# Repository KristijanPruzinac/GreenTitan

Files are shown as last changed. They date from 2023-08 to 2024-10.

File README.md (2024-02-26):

# GreenTitan
 GreenTitan is an open-source lawnmower project started in early 2023.
 The goal of the project is to enable makers to 3D print their own lawnmower that navigates using RTK GPS technology in well under a 1000$, because the commercial mowers are way too expensive.

The project currently uses the C94-M8P RTK GPS development board by u-blox, available through online retailers such as Mouser and others. When buying the board make sure to buy the correct variant of the board according to your region (https://www.u-blox.com/en/product/c94-m8p).



# Competition
As the project is open-source there is not much competition for it except for other open source projects. Unfortunately other projects seem to either feature software for an already made machine or only the 3d printed case, not both. My goal is to provide both with documentation to enable anyone to make it themselves.

# Credits
#### MODELS  
Ublox C94-Mp8-4 case with openings - CC BY 4.0 - Scorbin - https://www.thingiverse.com/scorbin/designs  
Einhell battery adapter - GNU GPL v3 - Hans - https://www.printables.com/social/193091-hans/about

#### SOFTWARE  
Recieve NAV_POSLLH message - iforce2d - https://www.youtube.com/watch?v=TwhCX0c8Xe0

#### LIBRARIES  
Adafruit MPU6050 - https://github.com/adafruit/Adafruit_MPU6050
AceSorting - https://github.com/bxparks/AceSorting

# Development process
The project is currently under development and expected to be finished in october.

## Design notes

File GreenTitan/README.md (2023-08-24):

# Arduino code  
This is the Arduino code for uploading to the ESP32 microcontroller.

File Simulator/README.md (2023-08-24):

# GreenTitan simulator

This is software written in Processing (java) sketchbook that is used to develop the GreenTitan project software. The issue with programming microcontrollers is often that it is harder to test them, especially with projects like robotic lawnmowers. It is for this reason that I decided to make this simulator so I can test mower software before deploying it with ESP32.

Feel free to use this if it is helpful to you in any way.



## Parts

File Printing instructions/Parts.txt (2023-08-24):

2x GW370 DC Worm Gear Motor (12V / 80RPM)
2x Shopping cart wheel (Height must be 10cm, Diameter when rotated should be less than 13cm, top hole should be less than 1cm)
1x C94 M8P RTK GPS (Choose correct region when buying)
M3 Allen screw 10mm & nut, 20x (8x)
M4 Allen screw 25mm & nut, 40x (34x)

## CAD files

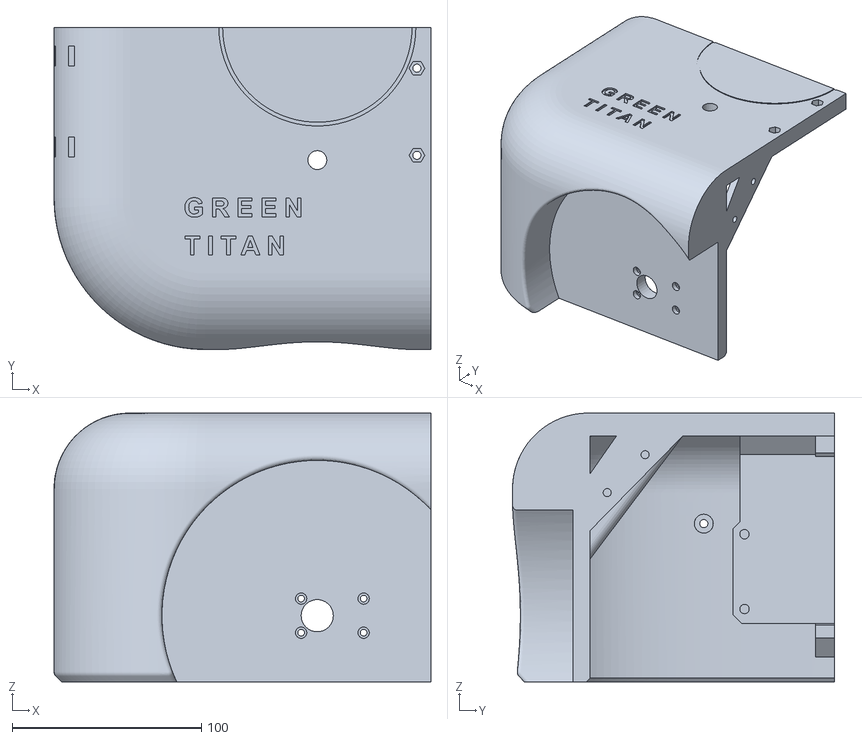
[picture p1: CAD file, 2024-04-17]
Printing instructions/Frame/Back/Right.stl
199.1 x 170.0 x 142.0

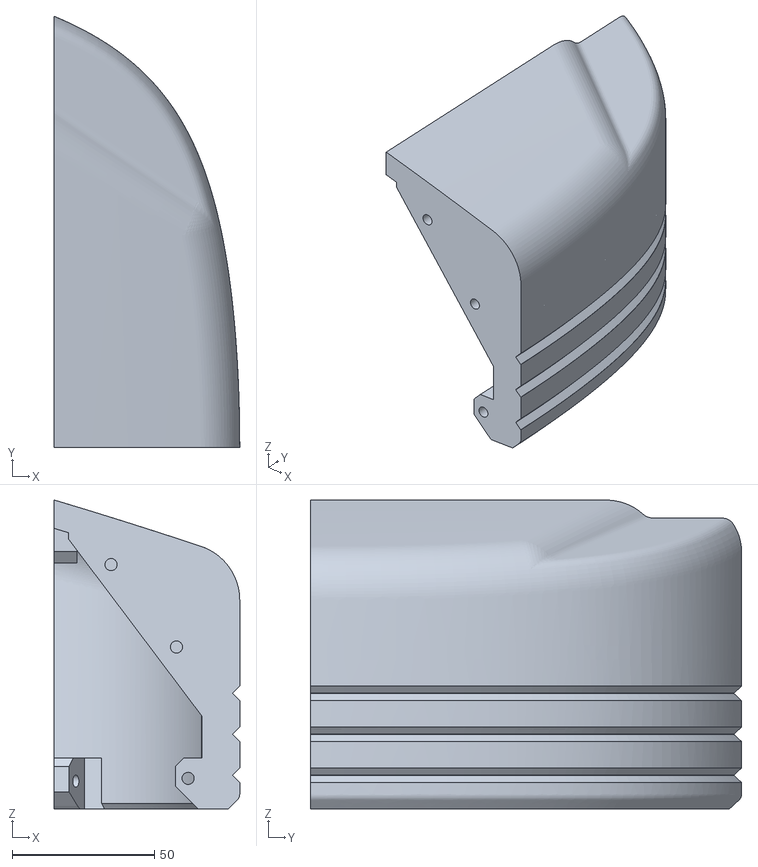
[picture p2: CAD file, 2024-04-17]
Printing instructions/Frame/Front/GreenTitanBumperLeft.stl
65.3 x 151.8 x 108.7

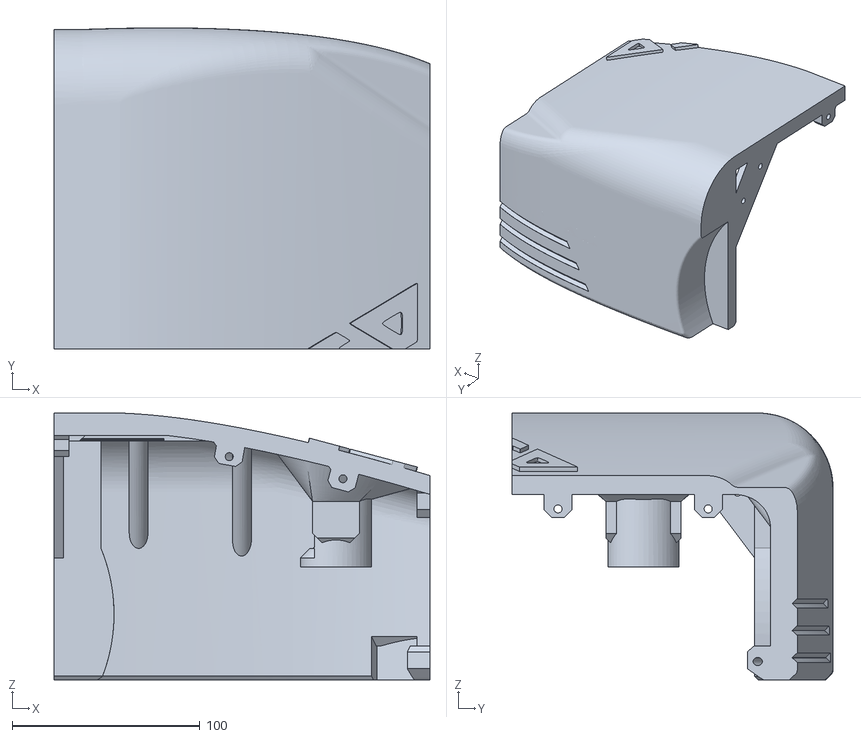
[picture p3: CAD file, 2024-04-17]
Printing instructions/Frame/Midsection/GreenTitanMidsectionLeft.stl
200.0 x 170.8 x 142.0

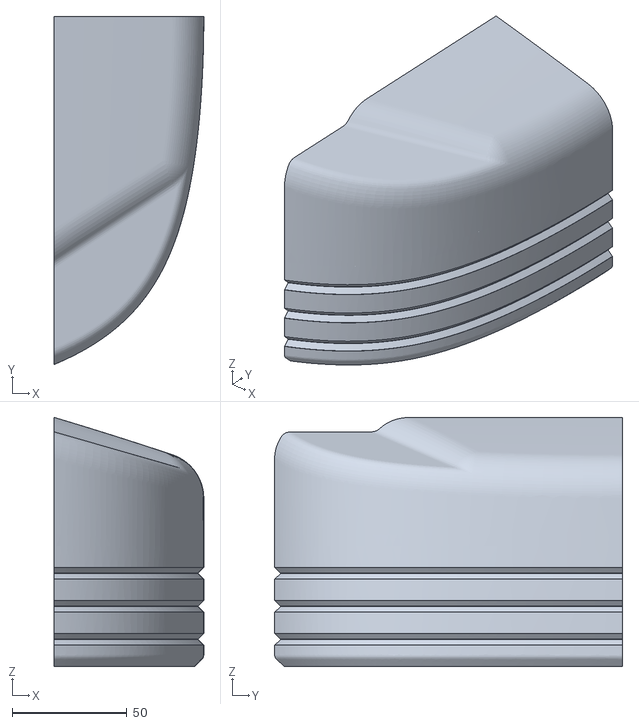
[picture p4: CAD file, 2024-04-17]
Printing instructions/Frame/Front/GreenTitanBumperRight.stl
65.3 x 151.8 x 108.7

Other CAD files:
Printing instructions/Frame/Back/Left.stl
Printing instructions/Frame/Midsection/GreenTitanMidsectionRight.stl

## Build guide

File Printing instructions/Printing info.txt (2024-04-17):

Used Ultimaker Cura 5.4.0 slicer

-----------------------------------------------------
REQUIRED

Minimum build plate area - 20cm * 20cm

-----------------------------------------------------
PRINT SETTINGS

Top / Bottom - 2 layers each
0.3mm layer height
Adhesion - Brim
Infill pattern - lines
Material - PLA, 200deg print temperature

-----------------------------------------------------
PART SETTINGS

Double battery adapter (Einhell) - Weight 24g, Printing time 1:30 | Infill 30%
C94 M8P Case - Weight 20g, Printing time 0:47 | Infill 20%

GENERAL SETTINGS: Infill 10% | Enable supports, Support placement Everywhere, Support structure Normal, Enable Support inteface False, Support density 10%, SUpport Z distance 0.3, Support XY distance 1.2

FRAME Front bumper - Weight 135g, Printing time 6:53
Support placement: Touching buildplate
Minimum support area: 500mm2

FRAME Side - Weight 360g, Printing time 18:49
Support placement: Everywhere
Minimum support area: 100mm2

FRAME Back - 353g, Printing time 20:28

Adjust minimum support area so supports are generated properly, but small holes aren't filled with supports (It is a pain to remove)

-----------------------------------------------------
ADVICE

Print every part so its interior side is facing the build plate, when supports are used on the exterior it looks pretty bad

The only parts I printed with exterior side facing build plate are the 2 back pieces and I printed their charging port facing the build plate, it looks tolerable

-----------------------------------------------------

TOTAL PLASTIC REQUIRED - LESS THAN 3KG

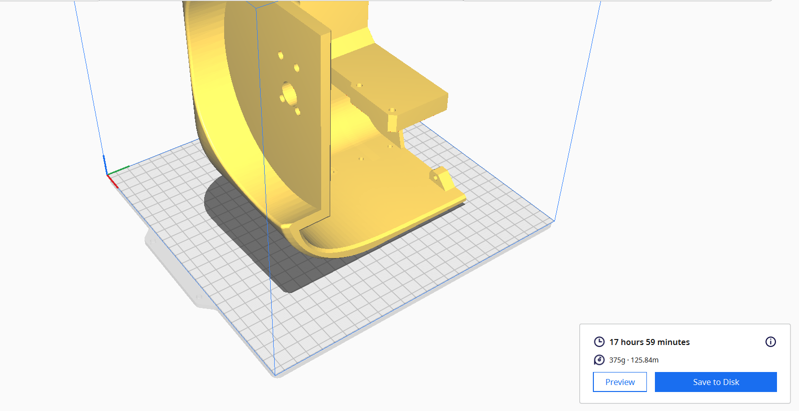
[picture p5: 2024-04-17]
Printing instructions/Frame/Back/Orientation.png

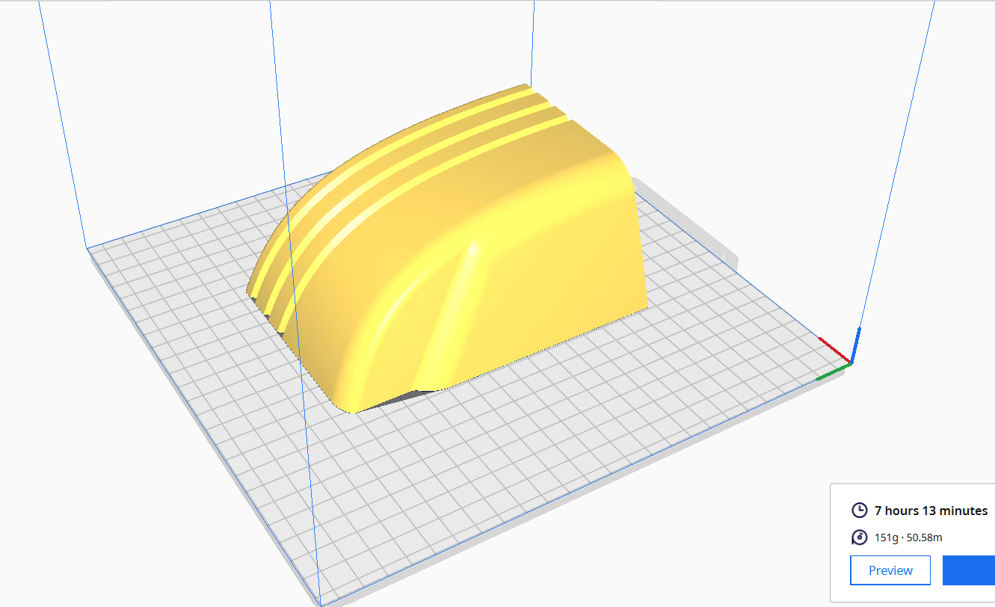
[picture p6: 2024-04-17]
Printing instructions/Frame/Front/Orientation.png

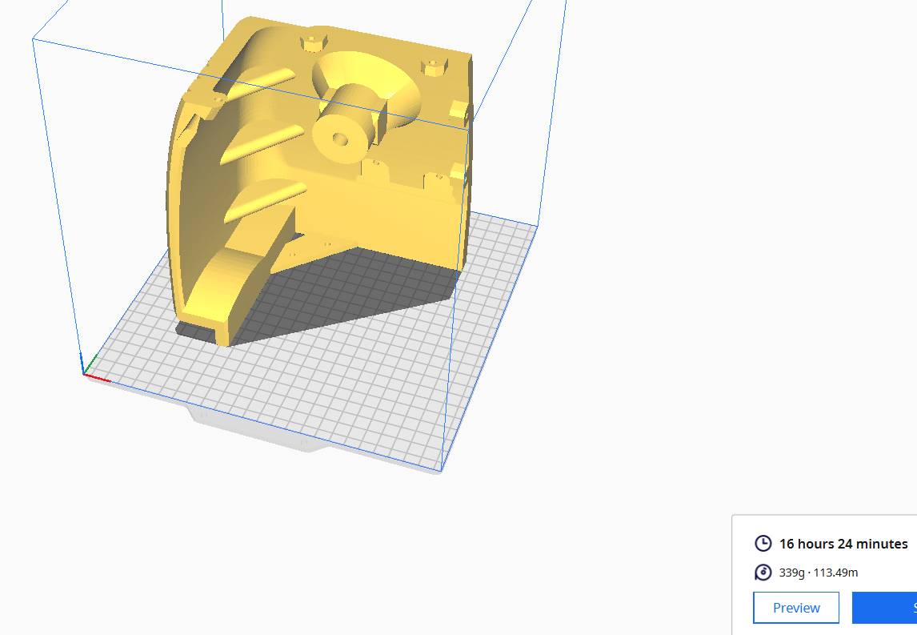
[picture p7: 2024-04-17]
Printing instructions/Frame/Midsection/Orientation.png

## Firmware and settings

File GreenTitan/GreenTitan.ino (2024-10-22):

// -------------------------------------------------------- DEFINITIONS ---------------------------------------------------------------
#include "Defines.h"

// -------------------------------------------------------- STATUS INDICATORS ---------------------------------------------------------------

int STATUS_BATTERY_LOW = false;
int STATUS_BATTERY_CHARGED = false;
int GPS_ACCURACY_STABLE = false;

// -------------------------------------------------------- CONFIGURATION ---------------------------------------------------------------

bool CONFIG_PATH = false;
bool CONFIG_BATTERY = false;
bool CONFIG_MOTORS = false;
bool CONFIG_GYRO = false;
bool CONFIG_RAIN_SENSOR = false;

// -------------------------------------------------------- GLOBALS ---------------------------------------------------------------

bool SETUP_COMPLETED = true;

int MOWER_OVERLAP = 15; //In cm
int MAX_DEVIATION = 50;
int BASE_LON = -5672328;
int BASE_LAT = 3376391;
int BASE_EXIT_LON = -5672328;
int BASE_EXIT_LAT = 3376391;

int GPS_ACC_THRESHOLD = 18;
int GPS_STABILITY_CHECK_DURATION = 300; //5 minutes

float BATTERY_LEVEL_MIN = 16;
float BATTERY_LEVEL_MAX = 18;

bool MOTOR_SIDE_INVERT = true;
bool MOTOR_LEFT_INVERT = true;
bool MOTOR_RIGHT_INVERT = false;
float MOTOR_OPTIMAL_VOLTAGE = 12;

//TODO: ADD TO CONFIG
bool IMU_INVERT = false;
float MOTION_ACC_FACTOR = 1.0;

SemaphoreHandle_t IMUMutex;
SemaphoreHandle_t GPSMutex;
SemaphoreHandle_t MotionMutex;

// -------------------------------------------------------- DEPENDENCIES ---------------------------------------------------------------

//Peripherals
#include "IMU.h"
#include "GPS.h"
#include "Battery.h"
#include "RainSensor.h"

//Program dependencies
#include "Functions.h"
#include "Algorithm.h"
#include "Configuration.h"

//Tasks
#include "MotionTask.h"
#include "BluetoothTask.h"
#include "SensorsTask.h"
#include "Motor.h"

// -------------------------------------------------------- INIT FUNCTIONS ---------------------------------------------------------------

void InitFreeRtos(){
  IMUMutex = xSemaphoreCreateMutex();
  GPSMutex = xSemaphoreCreateMutex();
  MotionMutex = xSemaphoreCreateMutex();

  //Motor task
  xTaskCreatePinnedToCore (
    MotorTask,     // Function to implement the task
    "MotorTask",   // Name of the task
    8192,      // Stack size in bytes
    NULL,      // Task input parameter
    2,         // Priority of the task
    NULL,      // Task handle.
    0          // Core where the task should run
  );

  //IMU task
  xTaskCreatePinnedToCore (
    IMUTask,     // Function to implement the task
    "IMUTask",   // Name of the task
    8192,      // Stack size in bytes
    NULL,      // Task input parameter
    2,         // Priority of the task
    NULL,      // Task handle.
    0          // Core where the task should run
  );

  //Sensors task
  xTaskCreatePinnedToCore (
    SensorsTask,     // Function to implement the task
    "SensorsTask",   // Name of the task
    8192,      // Stack size in bytes
    NULL,      // Task input parameter
    2,         // Priority of the task
    NULL,      // Task handle.
    0          // Core where the task should run
  );

  //Motion task
  xTaskCreatePinnedToCore (
    MotionTask,     // Function to implement the task
    "MotionTask",   // Name of the task
    8192,      // Stack size in bytes
    NULL,      // Task input parameter
    1,         // Priority of the task
    NULL,      // Task handle.
    0          // Core where the task should run
  );

  //Bluetooth task
  xTaskCreatePinnedToCore (
    BluetoothTask,     // Function to implement the task
    "BluetoothTask",   // Name of the task
    8192,      // Stack size in bytes
    NULL,      // Task input parameter
    0,         // Priority of the task
    NULL,      // Task handle.
    0          // Core where the task should run
  );
}

extern void InitMotors();
extern bool InitIMU();
extern void InitGPS();
extern void InitBattery();
extern void InitRainSensor();

// -------------------------------------------------------- PROGRAM START ---------------------------------------------------------------
void setup() {
  Serial.begin(SERIAL_BAUDRATE);
}

String Mode = "POWER_ON";
/*
POWER_ON

SETUP

START
RUNNING PAUSE
STOP
CHARGING
*/

void MainCharging();
void MainChargingStart();
void MainChargingStop();
void MainStop();
void MainPause();
void MainStart();
void MainRunning();
void MainPowerOn();
void MainSetup();

void loop(){
  if (Mode == "POWER_ON"){
    FileResult result = InitConfiguration();
    if (result != SUCCESS){
      Error("Configuration failed to initialize with error " + String(result));
    }

    Serial.println("Configuration loaded!");

    delay(200);

    InitMotors();
    if (!InitIMU()){
      Error("Gyro failed to initialize!");
    }
    //InitGPS();
    InitBattery();
    InitRainSensor();

    Serial.println("Peripherals initialized!");

    delay(200);

    if (!InitBluetooth()){
      Error("Bluetooth failed to initialize!");
    }
    else {
      Serial.println("Bluetooth initialized!");
    }

    delay(200);

    InitFreeRtos();

    Serial.println("FreeRtos initialized!");

    //TODO: Move to setup
    IMUCalibrate();

    delay(500);
    if (SETUP_COMPLETED){
      Mode = "RUNNING";
    }
    else {
      Mode = "SETUP";
    }
  }
  else if (Mode == "SETUP"){

  }
  else if (Mode == "START"){
    String message = BluetoothRead();

    if (message == "GPS_ACC"){
      BluetoothWrite(String(GpsGetAcc()));
    }
    else if (message == "CAPTURE_START") {
        AlgorithmCaptureStart();
        BluetoothWrite("Executed!");
    } else if (message == "GPS_POS"){
        //BluetoothWrite(String(GpsGetLon()) + " " + String(GpsGetLat()) + " " + String((int) IMUGetHeading()));
    } else if (message == "CAPTURE_BASE_POINT") {
        AlgorithmCaptureBasePoint();
        BluetoothWrite("Executed!");
    } else if (message == "CAPTURE_BASE_EXIT_POINT") {
        AlgorithmCaptureBaseExitPoint();
        BluetoothWrite("Executed!");
    } else if (message == "CAPTURE_NEW_OUTLINE") {
        AlgorithmCaptureNewOutline();
        BluetoothWrite("Executed!");
    } else if (message == "CAPTURE_NEW_POINT") {
        AlgorithmCaptureNewPoint();
        BluetoothWrite("Executed!");
    } else if (message == "REMOVE_OUTLINE") {
        bool result = AlgorithmCaptureRemoveOutline();
        BluetoothWrite(String(result));
    } else if (message == "REMOVE_POINT") {
        bool result = AlgorithmCaptureRemovePoint();
        BluetoothWrite(String(result));
    } else if (message == "CAPTURE_END") {
        bool result = AlgorithmCaptureEnd();
        BluetoothWrite(String(result));
    } else if (message == "GET_PATH_STRING"){
        BluetoothWrite(AlgorithmGetPathString());
    } else if (message == "SAVE_CONFIGURATION"){
        FileResult result = SaveConfiguration();
        BluetoothWrite(String(result));
    } else if (message == "MOWER_START"){
      Mode = "RUNNING";
    } else if (message == "TEST" || message == "GPS/GET/ACCURACY"){
      MotionSetTarget(GpsGetLon(), GpsGetLat() + 800);
    }
  }
  else if (Mode == "RUNNING"){
    MotorDriveAngle(0, FORWARD, 1.0);
    delay(1000);
    MotionSetTarget(1, -101);
    while (MowerIsInMotion()){
      delay(10);
    }
    MotorDriveAngle(0, FORWARD, 1.0);
    delay(1000);

    while (1){
      delay(100);
    }
  }
  delay(10);
}

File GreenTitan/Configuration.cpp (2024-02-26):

#include "Configuration.h"

#define FORMAT_LITTLEFS_IF_FAILED true

FileResult listDir(fs::FS &fs, const char *dirname, uint8_t levels) {
    File root = fs.open(dirname);
    if (!root) {
        return FAILED_OPEN;
    }
    if (!root.isDirectory()) {
        return NOT_A_DIRECTORY;
    }

    File file = root.openNextFile();
    while (file) {
        if (file.isDirectory()) {
            FileResult result = listDir(fs, file.path(), levels - 1);
            if (result != SUCCESS) {
                return result;
            }
        }
        file = root.openNextFile();
    }

    return SUCCESS;
}

FileResult createDir(fs::FS &fs, const char *path) {
    if (fs.mkdir(path)) {
        return SUCCESS;
    } else {
        return MKDIR_FAILED;
    }
}

FileResult removeDir(fs::FS &fs, const char *path) {
    if (fs.rmdir(path)) {
        return SUCCESS;
    } else {
        return RMDIR_FAILED;
    }
}

FileResult readFile(fs::FS &fs, const char *path, String &fileContent) {
    File file = fs.open(path);
    if (!file || file.isDirectory()) {
        return FAILED_OPEN;
    }

    while (file.available()) {
        char c = file.read();
        fileContent += c;
    }
    file.close();

    return SUCCESS;
}

FileResult writeFile(fs::FS &fs, const char *path, const char *message) {
    File file = fs.open(path, FILE_WRITE);
    if (!file) {
        return FAILED_OPEN;
    }
    if (file.print(message)) {
        file.close();
        return SUCCESS;
    } else {
        file.close();
        return FAILED_WRITE;
    }
}

FileResult appendFile(fs::FS &fs, const char *path, const char *message) {
    File file = fs.open(path, FILE_APPEND);
    if (!file) {
        return FAILED_OPEN;
    }
    if (file.print(message)) {
        file.close();
        return SUCCESS;
    } else {
        file.close();
        return APPEND_FAILED;
    }
}

FileResult renameFile(fs::FS &fs, const char *path1, const char *path2) {
    if (fs.rename(path1, path2)) {
        return SUCCESS;
    } else {
        return RENAME_FAILED;
    }
}

FileResult deleteFile(fs::FS &fs, const char *path) {
    if (fs.remove(path)) {
        return SUCCESS;
    } else {
        return DELETE_FAILED;
    }
}

FileResult InitConfiguration(){
  if(!LittleFS.begin(FORMAT_LITTLEFS_IF_FAILED)){
    return INIT_FAILED;
  }

  LoadConfiguration();

  return SUCCESS;
}

FileResult SaveConfiguration() {
    String ConfigWriteString = "";
    ConfigWriteString += "SETUP_COMPLETED " + String(SETUP_COMPLETED) + "\n";
    ConfigWriteString += "MOWER_OVERLAP " + String(MOWER_OVERLAP) + "\n";
    ConfigWriteString += "MAX_DEVIATION " + String(MAX_DEVIATION) + "\n";
    ConfigWriteString += "BASE_LON " + String(BASE_LON) + "\n";
    ConfigWriteString += "BASE_LAT " + String(BASE_LAT) + "\n";
    ConfigWriteString += "BASE_EXIT_LON " + String(BASE_EXIT_LON) + "\n";
    ConfigWriteString += "BASE_EXIT_LAT " + String(BASE_EXIT_LAT) + "\n";
    ConfigWriteString += "GPS_ACC_THRESHOLD " + String(GPS_ACC_THRESHOLD) + "\n";
    ConfigWriteString += "GPS_STABILITY_CHECK_DURATION " + String(GPS_STABILITY_CHECK_DURATION) + "\n";
    ConfigWriteString += "BATTERY_LEVEL_MIN " + String(BATTERY_LEVEL_MIN) + "\n";
    ConfigWriteString += "BATTERY_LEVEL_MAX " + String(BATTERY_LEVEL_MAX) + "\n";
    ConfigWriteString += "MOTOR_SIDE_INVERT " + String(MOTOR_SIDE_INVERT) + "\n";
    ConfigWriteString += "MOTOR_LEFT_INVERT " + String(MOTOR_LEFT_INVERT) + "\n";
    ConfigWriteString += "MOTOR_RIGHT_INVERT " + String(MOTOR_RIGHT_INVERT) + "\n";
    ConfigWriteString += "MOTOR_OPTIMAL_VOLTAGE " + String(MOTOR_OPTIMAL_VOLTAGE) + "\n";
    
    //Config status
    ConfigWriteString += "CONFIG_PATH " + String(CONFIG_PATH) + "\n";
    ConfigWriteString += "CONFIG_BATTERY " + String(CONFIG_BATTERY) + "\n";
    ConfigWriteString += "CONFIG_MOTORS " + String(CONFIG_MOTORS) + "\n";
    ConfigWriteString += "CONFIG_GYRO " + String(CONFIG_GYRO) + "\n";
    ConfigWriteString += "CONFIG_RAIN_SENSOR " + String(CONFIG_RAIN_SENSOR) + "\n";

    //Outlines
    ConfigWriteString += "ALGORITHM_PATH\n";
    ConfigWriteString += AlgorithmGetPathString();

    deleteFile(LittleFS, "/Configuration.txt");
    return writeFile(LittleFS, "/Configuration.txt", ConfigWriteString.c_str());
}
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

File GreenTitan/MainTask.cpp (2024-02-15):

#include "MainTask.h"

/*
int pointsCount = 0;
int gcodeIndex = 0;
int pointsX[50];
int pointsY[50];

//Parse bluetooth messages
void MainParseBluetooth(){
  while (true){
    String message = BluetoothRead(); if (message.length() == 0 || message.equals("")){ break; }

    //Count / characters
    int co = 0;
    for (int i = 0; i < message.length(); i++) {
      if (message.charAt(i) == '/') {
        co++;
      }
    }
    if (co < 2){break;} //Invalid message

    String MessageGroup = message.substring(0, message.indexOf('/'));
    message = message.substring(message.indexOf('/') + 1); // Update message to remove the first part

    String ActionGroup = message.substring(0, message.indexOf('/'));
    message = message.substring(message.indexOf('/') + 1); // Update message to remove the second part

    String DataGroup = message;

    //STATUS ------------------------------------------
    if (MessageGroup == "STATUS") {
      if (ActionGroup == "GET") {
        Respond("STATUS", MowerStatus);
      }
      else if (ActionGroup == "SET") {
        if (DataGroup == "RUNNING") {
          MowerResume();
        }
        else if (DataGroup == "PAUSED") {
          MowerPause();
        }

        Respond("STATUS", MowerStatus);
      }
    }
    else if (MessageGroup == "MOTOR") {
      if (ActionGroup == "SET") {
        if (DataGroup == "LEFTFORWARD") {}
        else if (DataGroup == "LEFTBACKWARD") {}
        else if (DataGroup == "LEFTSTOP") {}
        else if (DataGroup == "RIGHTFORWARD") {}
        else if (DataGroup == "RIGHTBACKWARD") {}
        else if (DataGroup == "RIGHTSTOP") {}
        else if (DataGroup == "MAINSTART") {
          MotorMainOn();
        }
        else if (DataGroup == "MAINSTOP") {
          MotorMainOff();
        }
      }
      else if (ActionGroup == "MOVE") {
        if (DataGroup == "FORWARD") {
          MotorForward();
        }
        else if (DataGroup == "BACKWARD") {
          MotorBackward();
        }
        else if (DataGroup == "ROTATELEFT") {
          MotorTurnLeft();
        }
        else if (DataGroup == "ROTATERIGHT") {
          MotorTurnRight();
        }
        else if (DataGroup == "STOP"){
          MotorStop();
        }
      }
    }
    else if (MessageGroup == "GPS"){
      if (ActionGroup == "GET") {
        if (DataGroup == "ACCURACY") {
          Respond("GPS", String(posllh.hAcc));
        }
      }
    }
    else if (MessageGroup == "GCODE"){
      if (ActionGroup == "ADD") {
        if (DataGroup == "POINT") { //ADD NEW POINT
          pointsX[pointsCount] = posllh.lon;
          pointsY[pointsCount] = posllh.lat;

          pointsCount++;
        }
      }
      else if (ActionGroup == "RESET") {
        pointsCount = 0;
      }
      else if (ActionGroup == "START") {
        MowerExecutingPath = true;
        gcodeIndex = 0;
      }
    }
  }

  return;
}
*/

//TODO: Implement functionality
String Mode = "POWER_ON";
/* CHARGING STOP PAUSE START RUNNING POWER_ON SETUP*/

void MainCharging(){}
void MainChargingStart(){
  Serial.println("Charging start");
}
void MainChargingStop(){}
void MainStop(){Serial.println("Strayed from path (STOP)");}
void MainPause(){}
void MainStart(){}
void MainRunning(){}
void MainPowerOn(){
  //LoadConfiguration();
  //GenerateGcode();
}
void MainSetup(){}

char QueueBluetoothMainReceive(){
  char returnChar = NULL;
  xQueueReceive(BluetoothMainQueue, &returnChar, 50);

  return returnChar;
}

void QueueMainBluetoothSend(char receivedChar){
  xQueueSend(BluetoothMainQueue, &receivedChar, 50);
}

void MainTask(void* pvParameters){
  while (1){
    delay(10);
  }
}

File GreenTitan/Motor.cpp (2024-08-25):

#include "Motor.h"

// create the stepper motor objects
ContinuousStepper<StepperDriver> motorA;
ContinuousStepper<StepperDriver> motorB;

float MowerAngularDegreesToMotorSteps(float unit){
  //     PATH AROUND CIRCUMFERENCE TRAVELLED (CM)                     STEPS PER CM                2 MOTORS
  return ((unit / (360.0)) * (MOTOR_DIAMETER * PI)) * (MOTOR_STEPS_PER_REV / (WHEEL_DIAMETER * PI)) / 2;
}

void MotorDriveAngle(float angle, bool forward, float speedFactor = 1) {
  // SpeedFactor
  speedFactor = constrain(speedFactor, 0.0, 1.0);

  // Angle measured from North clockwise
  angle = constrain(angle, MOTOR_ANGLE_MIN, MOTOR_ANGLE_MAX);

  // Motor activation percentages
  float motorPercentLeft = (angle + 90.0) / 180.0; motorPercentLeft = constrain(motorPercentLeft, 0, 1);
  float motorPercentRight = 1 - (motorPercentLeft); motorPercentRight = constrain(motorPercentRight, 0, 1);

  // Switch sides
  if (MOTOR_SIDE_INVERT) {
    std::swap(motorPercentLeft, motorPercentRight);
  }

  // Calculate speeds for motors
  float speedA = MOTOR_MAX_SPEED * speedFactor * motorPercentLeft;
  float speedB = MOTOR_MAX_SPEED * speedFactor * motorPercentRight;

  if (!MOTOR_LEFT_INVERT) {
    motorA.spin(forward ? speedA : -speedA);
  } else {
    motorA.spin(forward ? -speedA : speedA);
  }

  if (!MOTOR_RIGHT_INVERT) {
    motorB.spin(forward ? speedB : -speedB);
  } else {
    motorB.spin(forward ? -speedB : speedB);
  }
}

void MotorRotate(float speedFactor) {
  // SpeedFactor
  speedFactor = constrain(speedFactor, -1.0, 1.0);

  int invertA = 1;
  int invertB = 1;

  // Rotate
  if (MOTOR_SIDE_INVERT) {
    speedFactor = -speedFactor;
  }

  if (MOTOR_LEFT_INVERT) {
    invertA = -invertA;
  }
  if (MOTOR_RIGHT_INVERT) {
    invertB = -invertB;
  }
  
  motorA.spin(invertA * MOTOR_MAX_SPEED * speedFactor);
  motorB.spin(-invertB * MOTOR_MAX_SPEED * speedFactor);
}

float motorASpeed = 0;
void MotorRotateAcceleration(float acceleration){
  int invertA = 1;
  int invertB = 1;

  // Rotate
  /*
  if (MOTOR_SIDE_INVERT) {
    direction = !direction;
  }
  */

  if (MOTOR_LEFT_INVERT) {
    invertA = -invertA;
  }
  if (MOTOR_RIGHT_INVERT) {
    invertB = -invertB;
  }

  motorASpeed += MowerAngularDegreesToMotorSteps(acceleration);
  if (motorASpeed > MOTOR_MAX_SPEED / 2) motorASpeed = MOTOR_MAX_SPEED / 2;
  if (motorASpeed < -MOTOR_MAX_SPEED / 2) motorASpeed = -MOTOR_MAX_SPEED / 2;

  if (motorASpeed > 0){
    motorA.spin(invertA * motorASpeed);
    motorB.spin(-invertB * motorASpeed);
  }
  else if (motorASpeed < 0) {
    motorA.spin(-invertA * motorASpeed);
    motorB.spin(invertB * motorASpeed);
  }
  else {
    motorA.stop();
    motorB.stop();
  }

  Serial.print(motorA.speed()); Serial.print(" "); Serial.println(motorB.speed());

  //Serial.println(motorASpeed);
  //Serial.println(motorA.getCurrentVelocityInStepsPerSecond());
}

void InitMotors() {
  pinMode(MOTOR_MAIN, OUTPUT);

  motorA.begin(MOTOR_A_STEP_PIN, MOTOR_A_DIR_PIN);
  motorB.begin(MOTOR_B_STEP_PIN, MOTOR_B_DIR_PIN);

  // Set acceleration
  motorA.setAcceleration(MOTOR_ACCELERATION);
  motorB.setAcceleration(MOTOR_ACCELERATION);
}

void MotorStop() {
  motorA.stop();
  motorB.stop();
}

void MotorMainOn() {
  digitalWrite(MOTOR_MAIN, HIGH);
}

void MotorMainOff() {
  digitalWrite(MOTOR_MAIN, LOW);
}

void MotorTask(void* pvParameters){
  String toSend = "";
  int counter = 0;
  while (1){
    TickType_t xLastWakeTime;
    const TickType_t xPeriod = pdMS_TO_TICKS(MILLIS_PER_SECOND / MOTOR_UPDATE_FREQUENCY);

    xLastWakeTime = xTaskGetTickCount();

    motorA.loop();
    motorB.loop();

    vTaskDelayUntil(&xLastWakeTime, xPeriod);
  }
}

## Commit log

2023-03-25 Switched to Bluetooth low energy
2023-04-17 Switch to different library
2023-08-17 Configuration loading added
    [config.txt]
2023-08-25 Update MainAlgorithm.pde
    TODO: Fix BASE functionality not working on last node of infill
    [MainAlgorithm.pde]
2023-08-26 Update Printing info.txt
2023-10-02 Freertos structure started
    [Configuration.h]
2024-01-26 Battery finished
2024-01-27 Finished battery, Started motor
2024-01-28 Motor finished
2024-02-10 Cleaned up unfinished code
    [Configuration.h]
2024-02-10 started split into .h and .cpp
    [Configuration.h]
2024-02-10 Algorithm compiled
    TODO: Test on Esp32 and integrate with LittleFS for config
2024-02-11 Switched array to std::vector, algorithm functional
2024-02-12 Configuration saving loading completed
    [Configuration.h]
2024-02-15 Started sensors task
    [Configuration.h]
2024-02-20 Sensors done for now
2024-02-20 Started coding motion
    TODO: Check if everything is in order, meanwhile re 3D print charger parts and model and print main motor blade part,
    Next:
    For rotation gyro is main azimuth, gps just calibrates it slightly with sensor fusion,
    For movement try to do basic movement for now and maybe later add acceleration and speed
2024-02-21 Azimuth from IMU tested, motion completed
2024-02-26 Rotation works, needs testing
    [Configuration.h]
2024-03-02 Seems to be going to some target
    Have to fix MotorDriveAngle so it drives at full speed
    Also have to check why gps data isnt being recieved
    [Defines.h, GreenTitan.ino, IMU.cpp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]
2024-03-06 Switched to compass (Getting readings)
    TODO: Compass calibration, better motion planning with angle calc (rotation speed)
2024-03-06 Hardcoded calibration
2024-08-13 Stable version, stepper control
    Working Gyro, GPS, Stepper motor control
    TODO: Implement and test straight line following
2024-08-25 Imu mower rotates to origin and line follows origin
    TODO: Correct IMU Azimuth using gps data
    [Defines.h, GreenTitan.ino, IMU.cpp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]
2024-08-26 FIRST SUCCESSFUL GYRO + GPS FUSION
    GPS corrects Gyro azimuth, tweaking needed
    [Defines.h, GPS.cpp, GreenTitan.ino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]
2024-08-26 Tweaked correction factor a bit, need more tweak
    [Defines.h]
2024-08-27 Further tweaked GPS to GYRO correction
    Current settings, takes time for azimuth to settle, but is stable when it does
    [Defines.h, MotionTask.cpp]
2024-08-27 Line following working, going wrong way
    TODO: Check problem with angles being 180 degrees rotated
    [Defines.h, GPS.cpp, MotionTask.cpp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]
2024-08-28 Heading direction fixed, angle function fixed
    [GPS.cpp, MotionTask.cpp]
2024-08-28 +-6cm accuracy on line following
2024-10-22 Working movement, need to fix gcode generator
    [Algorithm.cpp, GreenTitan.ino, MotionTask.cpp]
